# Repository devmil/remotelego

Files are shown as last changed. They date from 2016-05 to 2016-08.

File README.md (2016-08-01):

# Remote Lego project
This project contains all the bits needed to make a remote controllable (Lego) car model.

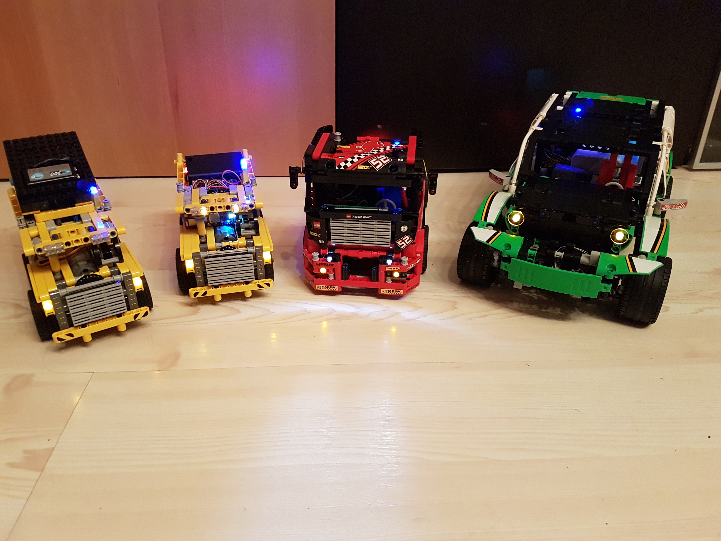
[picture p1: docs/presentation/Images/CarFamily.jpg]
Lego car family


For a guide how to modify and build the physical part of this project please refer to the project page on Hackster.io ([Project page](https://www.hackster.io/projects/9b59a9))
It contains instructions and a BOM for what is needed to get a remote controllable (Lego) car model.

The repository consists of two main parts:
##[Embedded](embedded/README.md)
This is where all the code resides that is needed for the embedded car electronics. It contains code for the mainboard as well as for the control board.

## Remote control applications
There are some remote control applications available for controlling the car model:
- [**Android / Android Wear**](android/README.md)
This simple app consists of a smartphone application and a wearable application
- [**Tizen wear**](tizen/wear/README.md)
Contains a Tizen Wear app
- [**WebApp**](https://github.com/devmil/remotelego_app)
The WebApp is hosted in a separate Repository as the distributed version gets hosted on GitHub. If you only want to control your model then you simply can use the already deployed version of this app.

# Getting started
After preparing your model you want to control and after creating a Mainboard (either by using a pre-made PCB or a perfboard) you can start off putting software onto your controllers.
Please refer to each components ReadMe to get a compile and flash guide:
- [ATMega32](embedded/Atmega/README.md)
- [RedBear DUO](embedded/RedBearDuo/README.md)
- [BLE Nano](embedded/BLENano/README.md)

For testing you can either use the WebApp (if you have an Android 6 device with Chrome and set it up correctly) or (more easier to set up) use the [Android app](android/README.md)

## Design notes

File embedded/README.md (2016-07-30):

# Remote Lego - Embedded
This subtree contains all the source code needed for the various embedded controllers that are part of the (Lego) remote controlled car.

##[Mainboard (Atmega)](Atmega/README.md)
The mainboard contains an Atmega microcontroller that is responsible for all the low level hardware communication. It configures timers to generate PWM signals, sets Pins for switching LEDs on and off and has some additional mechanisms to ensure that the car isn't driving away when the connection is lost or the control board hangs up :)
It gets controlled by the RedBear Duo (or any other controller you might use) via serial commands.

##[RedBear Duo](RedBearDuo/README.md)
The Duo is the communication partner for all remote controls. It provides the Bluetooth service needed for communication with the model and it contains all the car specific information (in form of profiles) like maximum steering angle, supported features, steering offset, ...

##[BLE Nano](BLENano/README.md)
This little helper has only one task: Broadcast the Eddystone advertising package. The software for it is designed in a way that it is generic and receives the URI to broadcast via serial commands.

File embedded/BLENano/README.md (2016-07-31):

# Remote Lego - Embedded - Control board (BLE Nano)

The BLE Nano is a Eddystone Broadcaster. It gets the URI to broadcast via UART following the same communication protocol used between RedBear DUO and the Mainboard.

For a guide how to set up the Arduino IDE to work with the BLE Nano see this web page: https://github.com/RedBearLab/nRF51822-Arduino

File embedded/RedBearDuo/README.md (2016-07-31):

# Remote Lego - Embedded - Control board (RedBear DUO)

Control board

The RedBear duo is the brain of the car models. It contains all the car specific logic and is the communication partner for the remote control. It implements the GATT service to expose the car models features.

## Preparation
In order to flash the software to the RedBear duo you have to install the Arduino IDE, set up the correct RedBear blugin and flash the correct firmware to the DUO.

For a Getting Started guide that covers the installation of Arduino and the RedBear plugin refer to this web page: [https://github.com/redbear/Duo/blob/master/docs/getting_started_with_arduino_ide.md](https://github.com/redbear/Duo/blob/master/docs/getting_started_with_arduino_ide.md)

Please make sure that you select the correct version of the plugin. The version the current code is tested with is mentioned in the LegoControl.ino file on the top.
To isntall the correct firmware for the selected plugin version just use the Arduino mechanism mentioned in the Getting Started guide to flash the firmware.

Additionally you need to install an stl port for Arduino as the lego car code uses standard types (shared_ptr, vector). There is a zip file containing the Arduino in the repository but you can just follow this guide to download and install the stl port:
[https://github.com/vancegroup/stlport-avr/wiki](https://github.com/vancegroup/stlport-avr/wiki).

## Flash
After you have set up the environment and installed the correct firmware version you should be ready to go. Just hit "Upload" in the Arduino IDE to compile the project and upload it to the RedBear Duo.

## Inner workings
The RedBear Duo code consists of

1. The LegoControl.ino file
This file is only used as an entry point. The system initialization is triggered there and the main cycle gets distributed. All other files are C++ files.

2. AVRCommunication.
This module encapsulates all communication logic with the AVR. It exposes the available commands via CommandData factory methods so that no other module has to know the inner structure of these commands. It also handles the serial protocol used to communicate with the AVR.

3. BLECommunication
This module contains the GATT service configuration and the implementation of the Service and the Characteristics. Here the Link between the Bluetooth communication and the model is made.

4. BlinkControl
This module handles the Blink logic. It controls the central Blink timer and triggers a re-send of the AVR telegrams

5. Bluetooth
This modules creates an abstraction layer on top of the Bluetooth API provided by RedBear. It works with Service and Characteristic classes, handles the advertisement bytes and routes read/write requests to the correct characteristic instance.

6. LegoCarModel
The LegoCarModel is the heart of the car. It contains all the business logic and contains the current car state. Any changes made to the state of the model get translated into according AVR telegrams and get sent to the Mainboard.

7. NanoCommunication
This module encapsulates the communication with the BLW Nano. It basically sends the Eddystone URI to the BLE Nano (or better: ensures that the current URI is transmitted to the BLE Nano). It does so cyclic as the protocol isn't as strict as with the AVRCommunication so that the timeouts are smaller and therefore a immediate transmittion can't be guarantieed. This has been done to not disturb the AVR communication when there is a problem with the BLE Nano communication (e.g. when the module is missing)

8. Profiles
Each car model has its own specifics. These specifics are provided by instances of "ICarProfile". Each car model that we have controlled using this mechanism already has a profile. For the code to compile you have to choose a profile (or create your own).
Some of the specifics are: 
 - maximum steering angle
 - steering offset
 - steering inverted?
 - Available features

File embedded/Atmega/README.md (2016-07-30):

# Remote Lego - Embedded - Mainboard (Atmega)

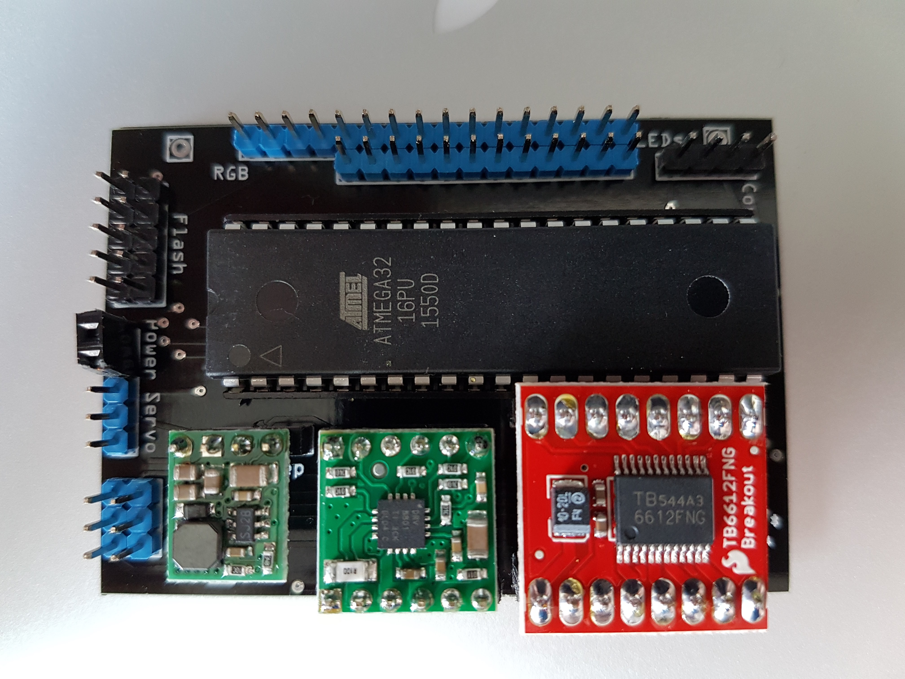
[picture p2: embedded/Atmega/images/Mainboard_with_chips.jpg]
Mainboard


The Mainboard is designed to be generic. It doesn't have any car specific logic. For example: It even doesn't have the logic to switch on the reverse driving lights when driving backwards. 

The idea behind that is to have a fully generic Mainboard with a very stable software and (hopefully) no variance at all.

## Prerequisites
In order to build and flash the software to the AVR you need to install:
###AVR toolchain
Installation depends on your development machine. For Mac just use homebrew and install it by executing:

`brew install avr-libc`

This toolchain should contain avr-gcc and avrdude
### Make
If you have a Mac make is part of XCode. Just make sure you have it installed.
On other machines you have to install make by using a package manager or setup.

###Burn AVR
The AVR has to be configured one time. To do that, plug the flash adapter cable to the mainboard and power it on. Please check the plug if the nose heads away from the mainboard (see picture)
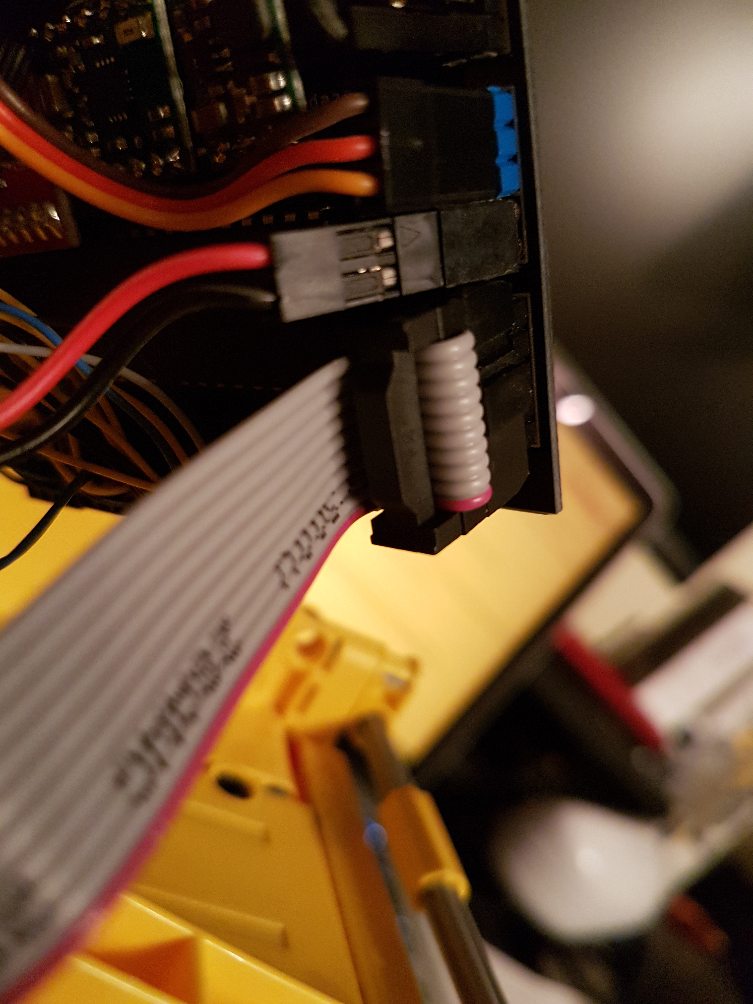
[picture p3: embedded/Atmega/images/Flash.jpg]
Flash plug

Use a Terminal application of your choice, go to the main directory and execute 

`make prepare_avr`

## Build
Open your favourite Terminal, go to the main directory and enter

`make all` or `make rebuild`

## Flash
Make sure you have connected the AVT flash USB device to the Mainboard and that you have powered it up. Please check the plug if the nose heads away from the mainboard (see picture)
Open your favourite Terminal, go to the main directory and enter

`make flash`

## How it works
The AVR gets commands via UART and executes them.

It also awaits a periodical ping from the control module otherwise it switches everything off (speed, steering, ...) to make sure that a control module crash doesn't lead to a car that drives away :)

The only thing the Mainboard persists is the steering offset. As soon as the Control board sends a steering offset the AVR stores it to the EEPROM. This is done to have no strange behavior during boot (The AVR is immediately up and centers the servo. When the control module is up it sends the offset which leads to another angle (when offset !=0).

The AVR uses all 4 timer channels. One for the main motor, two for the feature motors and one for the servo. The servo timer is also used to update the internal clock and to make periodical checks (like if the feature motor timeout has been reached)

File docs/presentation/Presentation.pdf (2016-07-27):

# PHYSICAL WEB MEETS WEB BLUETOOTH

## RC LEGO CAR PROJECT

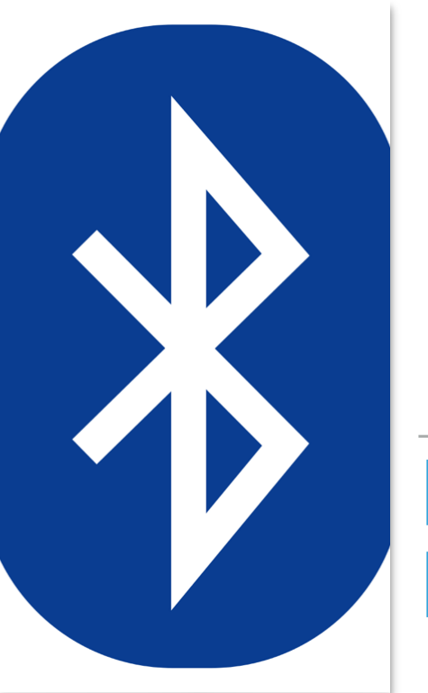
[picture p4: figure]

# BLUETOOTH BACKGROUND

BLUETOOTH BACKGROUND

GENERAL INFORMATION

▸ developed 1990
▸ standard for wireless device to device communication
▸ current version: v4.2
▸ „normal“ Bluetooth connection oriented (pairing)
▸ Bluetooth Low Energy (since v4.0) ad hoc communication possible

3

BLUETOOTH BACKGROUND

BLUETOOTH PROFILES

▸ Interface definitions. Samples are:
▸ A2DP (Advanced Audio Distribution Profile) - audio streaming
▸ OBEX-FTP - file transfer
▸ HID - Human Interface Device Profile
▸ PAN - Personal Area Network Profile ▸ GATT - Generic Attribute Profile

4

BLUETOOTH BACKGROUND

BLUETOOTH LOW ENERGY

▸ Since Bluetooth v4.0
▸ Optional (v4.0 devices don’t have to support BLE)
▸ Physical wireless communication is different for Bluetooth and BLE so most Bluetooth chips have two circuits
▸ Slaves send advertisement packages periodically
▸ only GATT profiles supported
▸ Android: since Version 4.3, iOS: since Version 5

5

BLUETOOTH BACKGROUND

BLUETOOTH GATT PROFILE

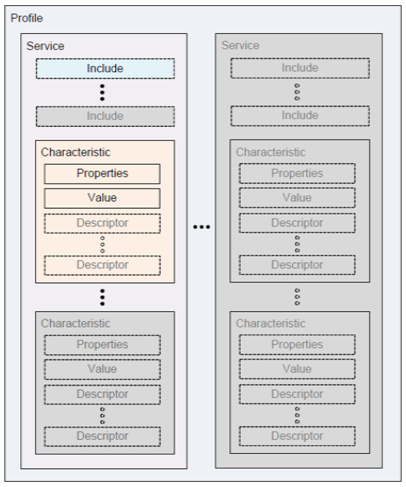
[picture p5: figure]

▸ A device implementing the GATT profile provides: ▸ 1..n services [UID]
▸ with 1..n characteristics [UID] ▸ read/write/readWrite
▸ Represents a value
▸ There are a number of standardized services (standardized UID):
▸ Battery Service
▸ Blood Preassure

▸ …

6

BLUETOOTH BACKGROUND

BLUETOOTH BEACONS

▸ Based on Bluetooth Low Energy

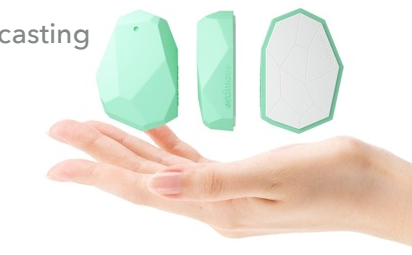
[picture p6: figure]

▸ Continuous advertisement package broadcasting ▸ Protocols
▸ iBeacon (Apple): UID advertisement
▸ AltBeacon: UID advertisement
▸ URIBeacon: URL advertisement
▸ Eddystone (Google): UID, URL or TLM advertisement
▸ Clients use the beacons to react to their presence and / or data

7

BLUETOOTH BACKGROUND

PHYSICAL WEB

▸ Initiated by Google

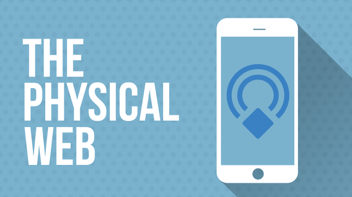
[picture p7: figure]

▸ Idea: Interaction with a nearby device should be possible without installing anything on the client device
▸ Based on Eddystone Beacons (currently, the idea is independent from that)
▸ Integration in Android devices is currently rolling out (newest Google Play Services -> Nearby)
▸ Usable with the Physical Web app (Android) or Google Chrome (iOS)

8

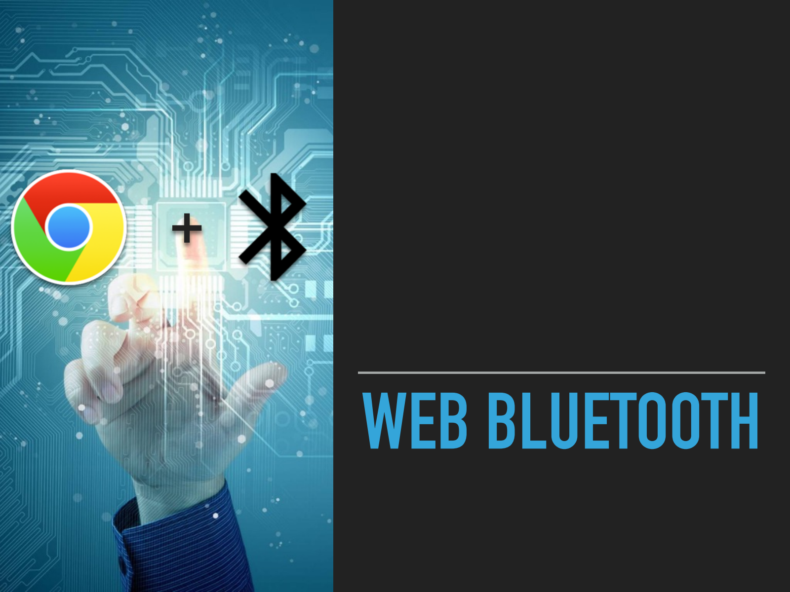
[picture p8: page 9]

# WEB BLUETOOTH

+

WEB BLUETOOTH

CORNERSTONES

▸ Standard for interacting with BLE devices from a web page via JavaScript (WebApp)
▸ Developed as a community team managed from the W3C ▸ No standard yet and no plans in sight
▸ Many years will pass until WebBluetooth is a standard and integrated in all common browsers and platforms

10

WEB BLUETOOTH

CURRENT PROGRESS

▸ Google has done a first reference implementation in Chrome/ Chromium
▸ Work in progress: API can change any time
▸ Only a hand full of platforms supported (27.06.16: Android, Chrome OS, Linux, planned: Windows, MacOS, iOS: when Apple adds WebBluetooth to its WebKit)
▸ Microsoft is thinking about an implementation („under consideration“)
▸ Apple didn’t release any statement regarding WebBluetooth yet

11

WEB BLUETOOTH

SECURITY

▸ Protection against abusing this API is the primary goal of the specification
▸ Requirement: User has to actively interact with the device to provide a web application access to a BLE device
▸ The web app can’t see all BLE devices. It only gets access to the device the user selected (so that location determination isn’t possible using this API)
▸ API only can be used having a secure connection (https)

12

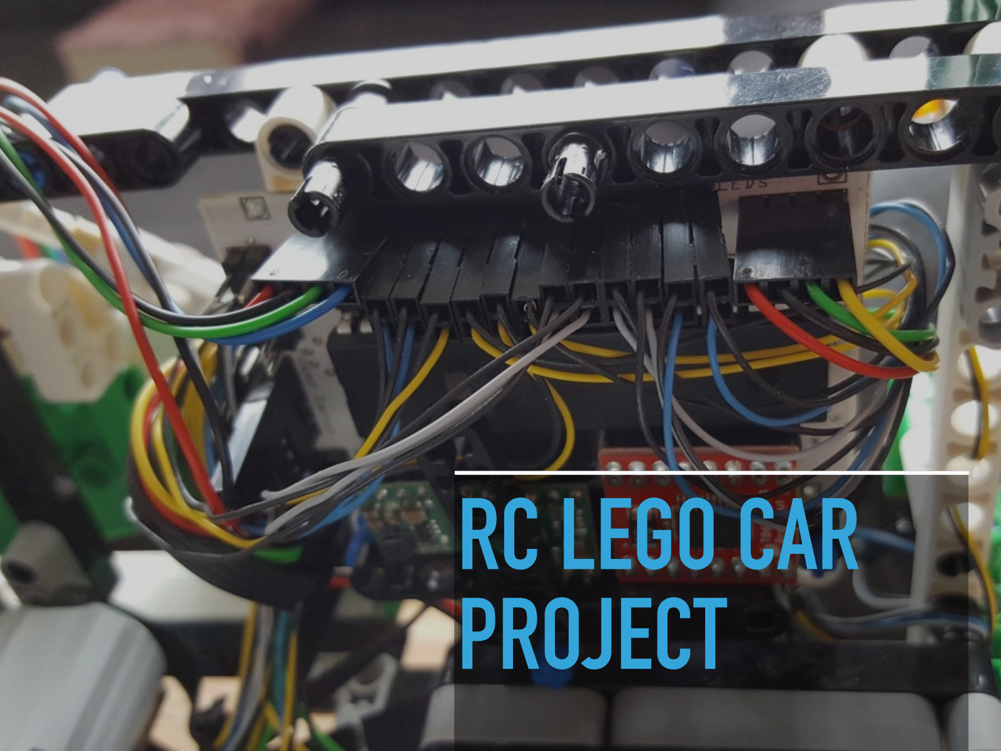
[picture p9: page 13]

# RC LEGO CAR PROJECT

RC LEGO CAR PROJECT

INTENTION

▸ Combine WebBluetooth with the ideas from the Physical Web
▸ Controlling a device
▸ without installing an app
▸ without having the device to be connected to the internet
▸ using state of the art web technology like offline caching

14

RC LEGO CAR PROJECT

WHY LEGO?

▸ First try: Switching a LED on and off
▸ BLE Slave: Raspberry Pi (NodeJS)
▸ Not very impressive => the idea to control a Lego Technic car has been born
▸ Project mutated from a web to a electronic project

15

RC LEGO CAR PROJEKT

VARIANTS

▸ Over the course of the project different variants were implemented ▸ BLE Slave (Car logic):
▸ Raspberry Pi (NodeJS)
▸ Intel Edison (NodeJS)
▸ RedBear Duo (Arduino) and ATMega32 (C)
▸ BLE Master (Remote control)
▸ Android App (Java, Android Framework)
▸ Android Wear App (Java, Android Framework)
▸ Tizen Wear App (HTML 5, TAU [Tizen Advanced UI]) ▸ Web App (HTML 5, AngularJS 2)

16

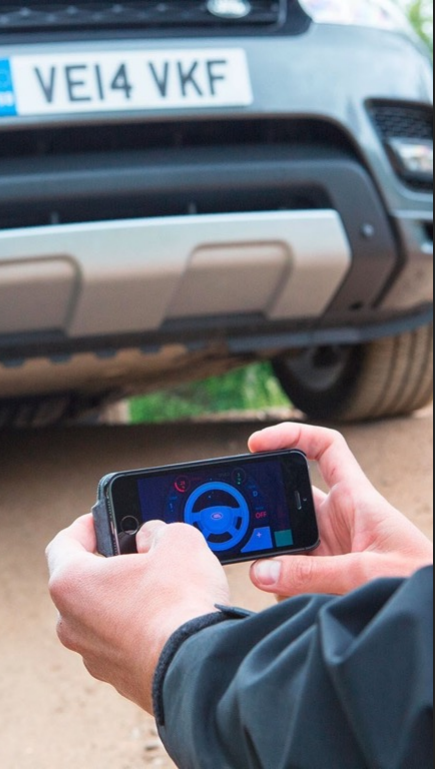
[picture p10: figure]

# REMOTE CONTROL

## RC LEGO CAR PROJECT

RC LEGO CAR PROJECT - REMOTE CONTROL

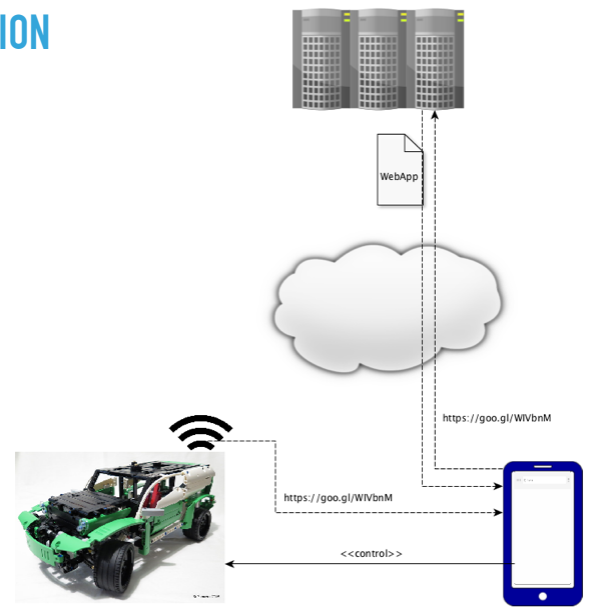
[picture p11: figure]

CONNECTION

18

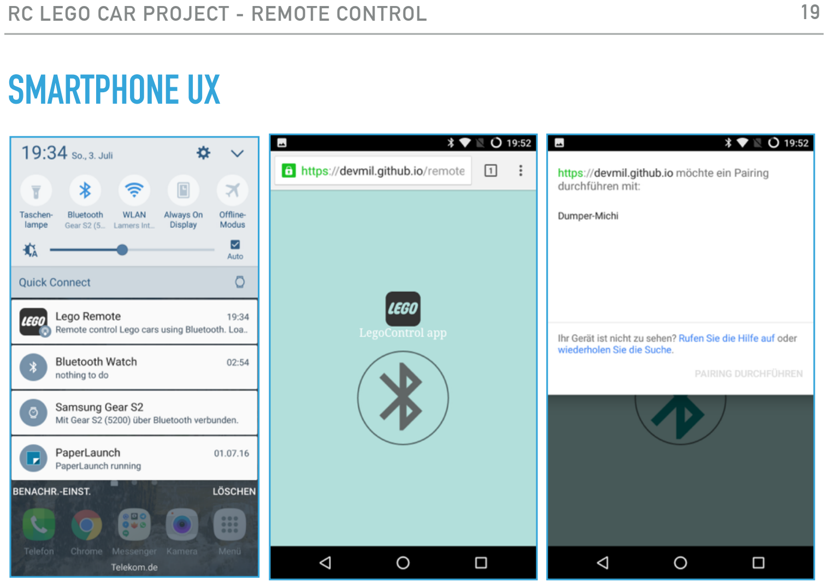
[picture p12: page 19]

RC LEGO CAR PROJECT - REMOTE CONTROL

SMARTPHONE UX

19

RC LEGO CAR PROJECT - REMOTE CONTROL

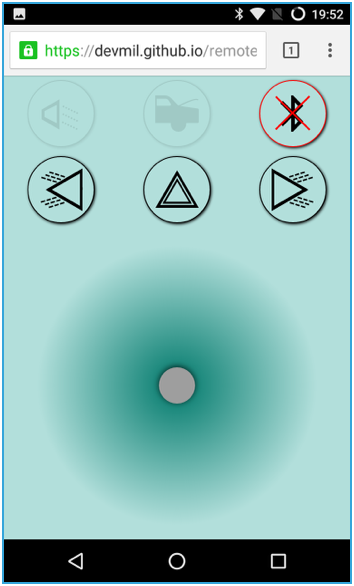
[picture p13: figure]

WEBAPP

▸ Typescript
▸ AngularJS 2
▸ Connects to the Lego control service (via UID) ▸ Writes data to characteristics:
▸ SpeedCharacteristic
▸ SteeringCharacteristic
▸ TrunkCharacteristic
▸ FrontLightCharacteristic ▸ BlinkCharacteristic

20

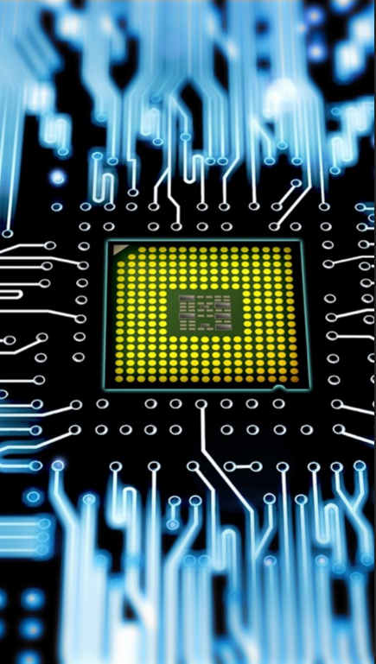
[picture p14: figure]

# CAR ELECTRONICS

## RC LEGO CAR PROJECT

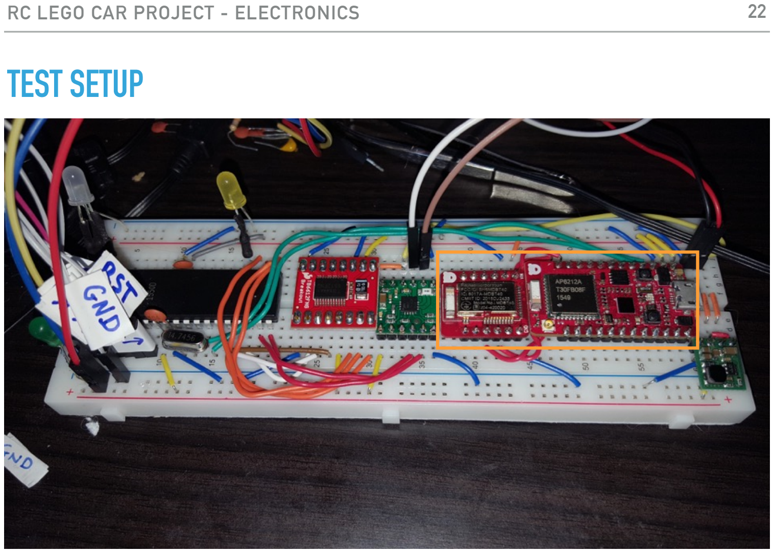
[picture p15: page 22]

RC LEGO CAR PROJECT - ELECTRONICS

TEST SETUP

22

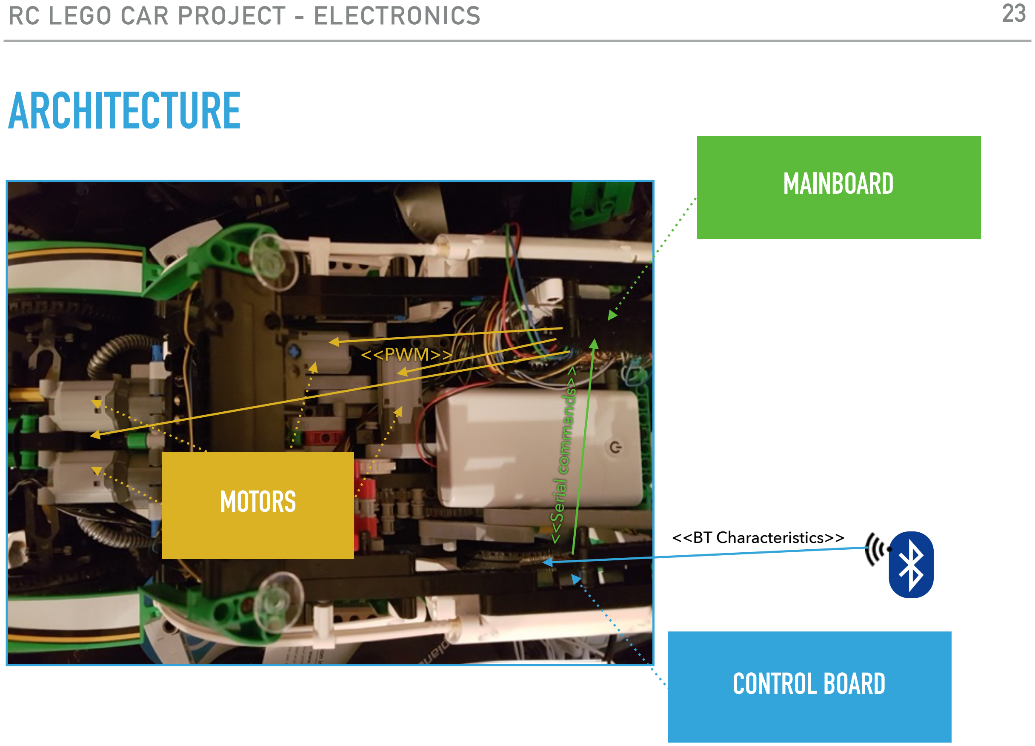
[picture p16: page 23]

RC LEGO CAR PROJECT - ELECTRONICS

ARCHITECTURE

23

<<Serial commands>>

<<BT Characteristics>>

<<PWM>>

CONTROL BOARD

MAINBOARD

MOTORS

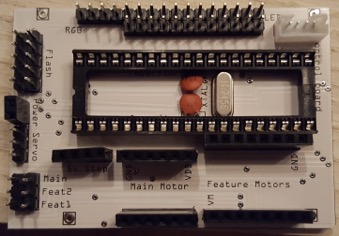
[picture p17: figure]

RC LEGO CAR PROJECT - ELECTRONICS

MAINBOARD

▸ Hardware control
▸ No car specific logic

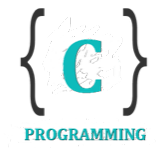
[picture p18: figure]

▸ Timer for PWM signals
▸ Parts:
▸ ATMega32
▸ 5V Step down regulator

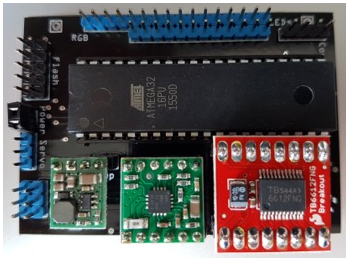
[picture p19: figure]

▸ H bridges (single for main motor, dual for feature motors) ▸ Receives commands via UART from control board

24

RC LEGO CAR PROJECT - ELECTRONICS

MAINBOARD CIRCUIT

25

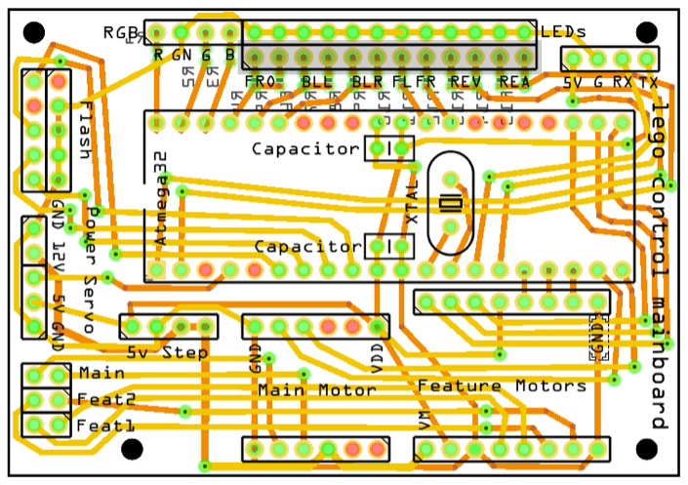
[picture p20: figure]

RC LEGO CAR PROJECT - ELECTRONICS

CONTROL BOARD

▸ Provides the BT service
▸ Contains the car logic
▸ what does „open trunk“ mean?

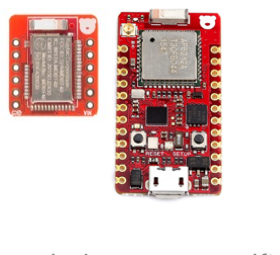
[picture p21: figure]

▸ Blink control (sends LED on/off to the mainboard, controls the timings itself) ▸ has a car specific profile
▸ Maximum steering angles
▸ is steering inverted?
▸ is Trunk, Front light, Blinking, … supported? ▸ Broadcasts the Eddystone telegram that contains the URL to the WebApp

26

RC LEGO CAR PROJECT - ELECTRONICS

INFORMATION FLOW

27

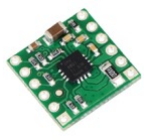
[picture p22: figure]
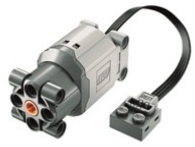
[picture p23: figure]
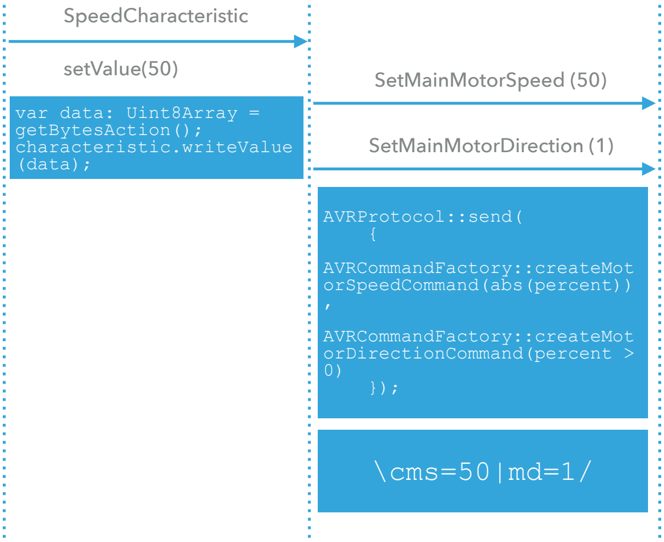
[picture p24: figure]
SpeedCharacteristic; setValue(50); var data: Uint8Array = getBytesAction(); characteristic.writeValue (data);; SetMainMotorSpeed (50); SetMainMotorDirection (1); AVRProtocol::send( {; AVRCommandFactory::createMot orSpeedCommand(abs(percent)) ,; AVRCommandFactory::createMot orDirectionCommand(percent > 0); \cms=50|md=1/

50% PWM (12V)

50% PWM (12V)

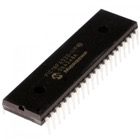
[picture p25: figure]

50% PWM (5V)

Direction Pin High

float value = (motor-
>timerMax *
percent) / 100;
*motor->
timerCounterRegister8
= (uint8_t)value;
Pin_setValue(&motor->
pinDirection1,
directionVal);


# DEMO

## RC LEGO CAR PROJECT

RC LEGO CAR PROJECT - SOURCES

SOURCES

▸ Wikipedia
▸ Bluetooth: https://de.wikipedia.org/wiki/Bluetooth
▸ BLE: https://de.wikipedia.org/wiki/Bluetooth_Low_Energy
▸ Bluetooth developer
▸ GATT: https://developer.bluetooth.org/TechnologyOverview/Pages/GATT.aspx (https://developer.bluetooth.org/TechnologyOverview/Pages/GATT.aspx)
▸ Physical Web
▸ https://google.github.io/physical-web/

29


RC LEGO CAR PROJECT - SETUP

SETUP (ANDROID 6.0, CHROME)

30

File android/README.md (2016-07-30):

# Remote Lego - Android remote control
App screenshot

The lego remote control app contains three modules:

1. **app**
The Android smartphone application. It needs Android Lollipop+ (21+) because it uses the BLE API.

2. **legologic**
This module gets used by the app and the legowear module. It contains the communication bits with the remote car and the control UI.

3. **legowear**
The Android wear application using (as well as the app) the legologic bits to display the control UI and communicating with the (Lego) car model

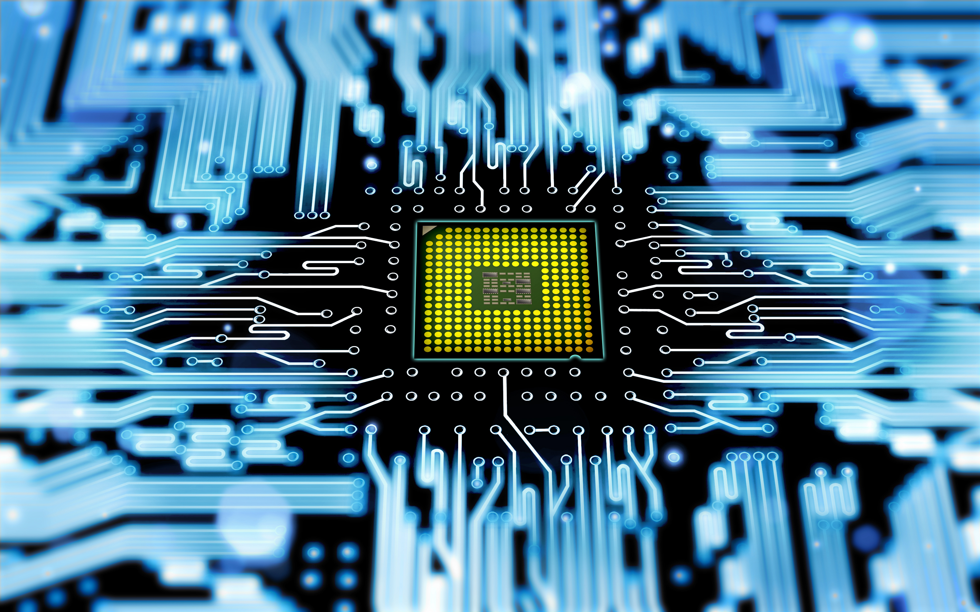
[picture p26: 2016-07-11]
docs/presentation/Images/Electronics.jpg

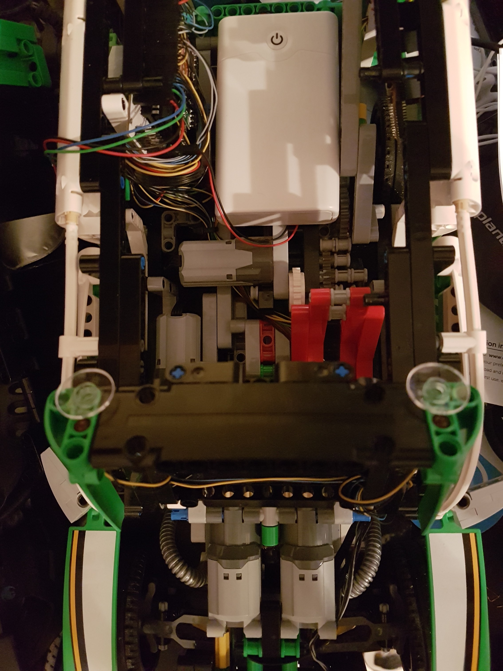
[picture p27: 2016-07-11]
docs/presentation/Images/RC Car Overview.jpg

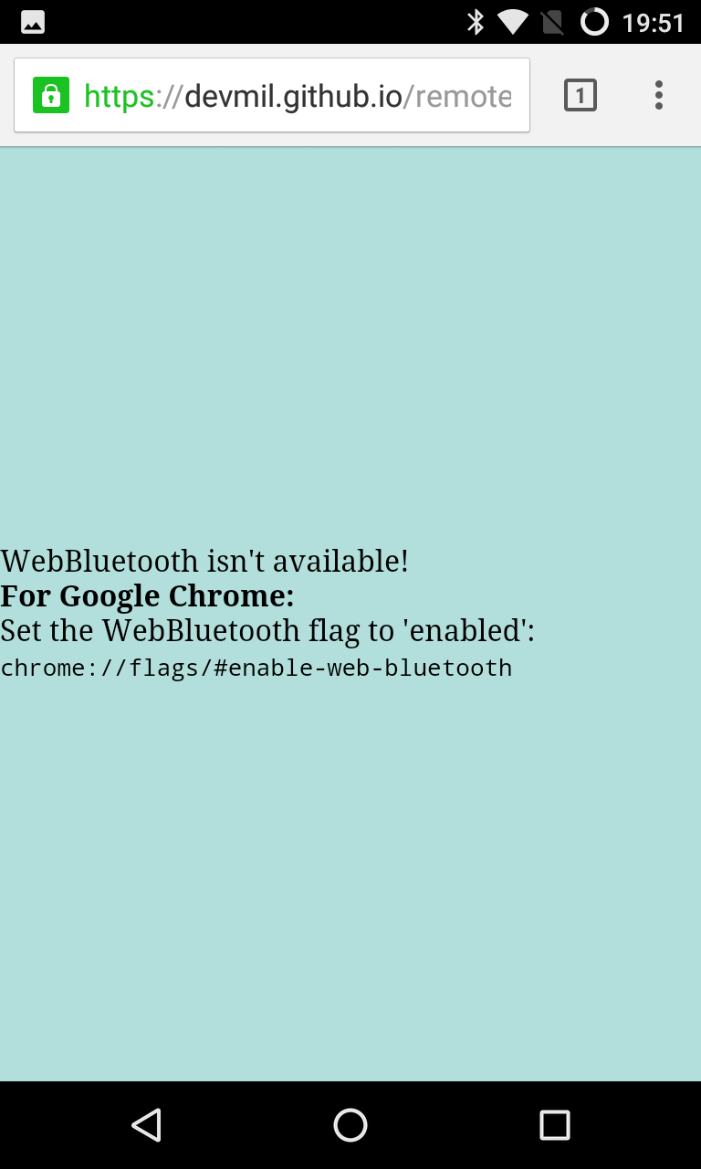
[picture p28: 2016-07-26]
docs/presentation/Images/Chrome_1_Message.png

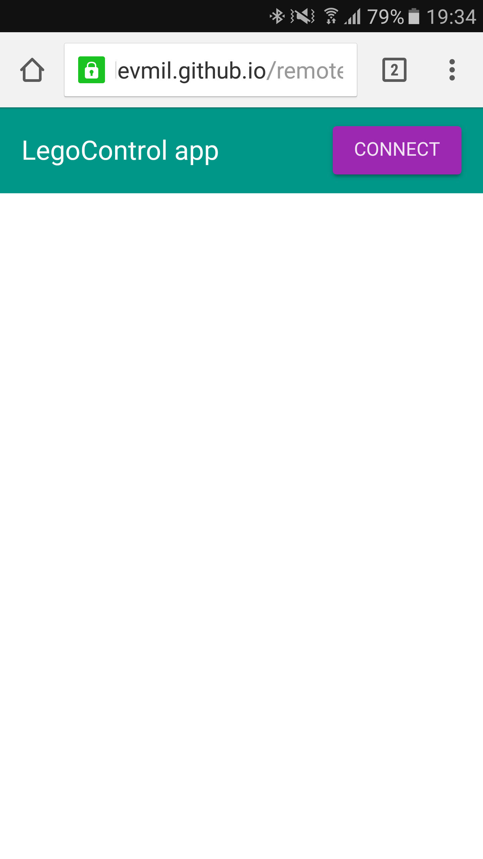
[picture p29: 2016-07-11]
docs/presentation/Images/Screenshot_20160703-193430.png

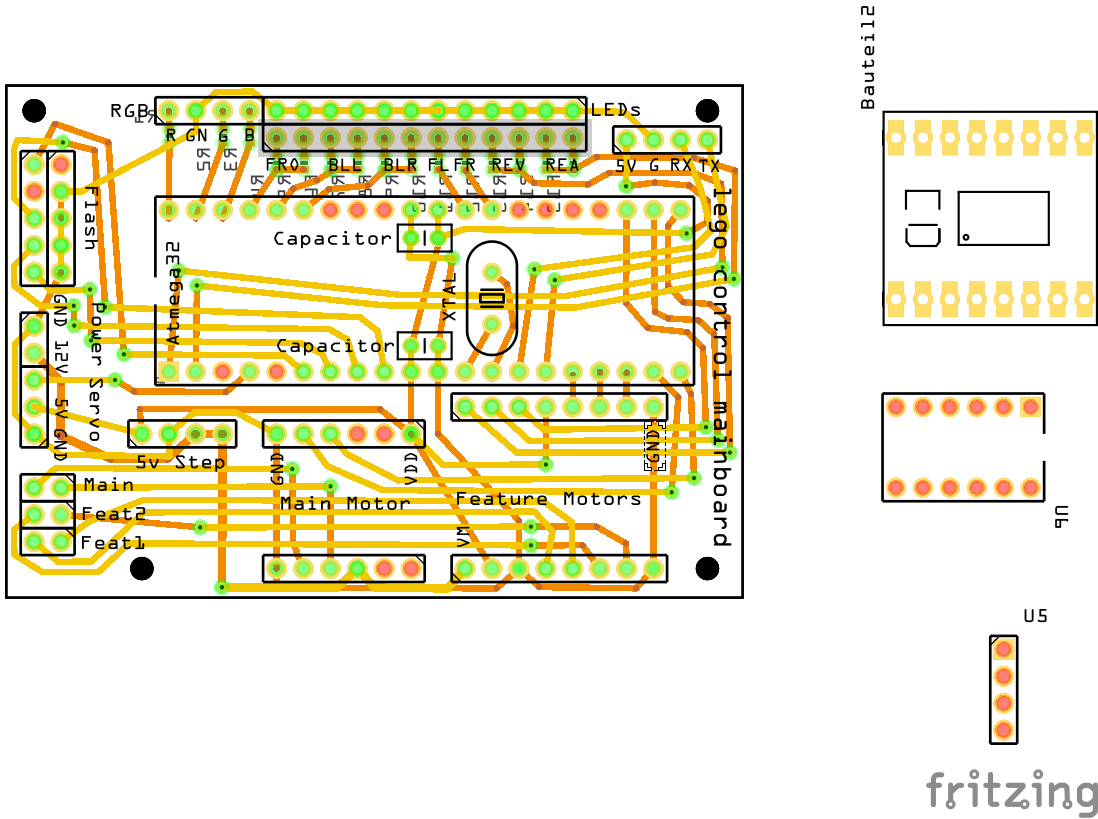
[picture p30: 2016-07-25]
docs/presentation/Images/Mainboard_Leiterplatte.png

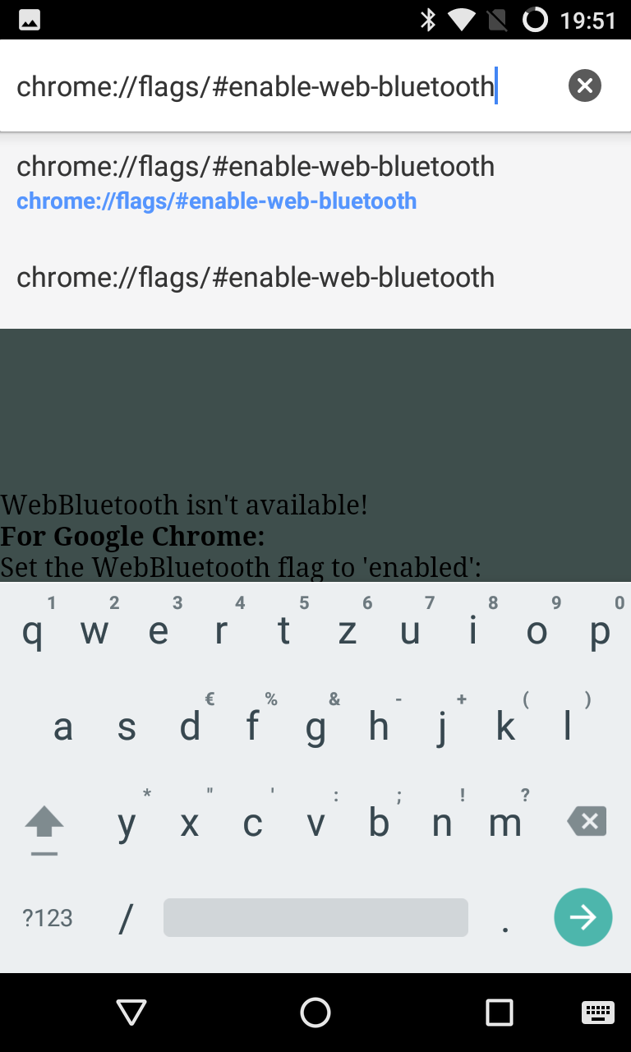
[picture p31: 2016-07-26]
docs/presentation/Images/Chrome_2_Flags.png

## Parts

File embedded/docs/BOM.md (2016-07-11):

#Lego RC electronics BOM

##General
- cables in different colors (Mainboard -> LEDs, Motors, Control board)
- a bunch of Dupont plugs (2 pin, 4 pin)
- Dupont capable crimping tool
- soldering iron & accessories
- AVR flash adapter

##Control Module variant a (Redbear Duo, BLE Nano)
- Redbear Duo (25€)
- BLE Nano (15€)
- circuit board
- lacquered wire for soldering connections on the circuit board

##Control module variant b (Raspberry Pi)
- Raspberry Pi 1/2/3 (35€)
- two RPI compatible Bluetooth USB dongles (10€ each)
- Battery pack to power the RPi (10€)

##Mainboard
- Atmel ATMega32 16PU or pin compatible (6€)
- Pololu 5V, 600mA Step-Down Voltage Regulator (D24V6F5) (6€)
- Pololu Single Brushed Motor Driver Carrier (DRV8801) (Main motor) (6€)
- Sparkfun Dual Motor Driver 1A TB6612FNG (9€)
- 14,745 MHz quartz
- 2x 100nF capacitor
- 15x SMD resistors (470 Ohm)
- a bunch of pin headers (male/female)
- a bunch of LEDs (2x front light, 2x back light, 2x rear light, 2x front fog lights, 4x blinking lights, 1x RGB state led)

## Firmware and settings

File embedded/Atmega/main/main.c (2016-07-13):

#include <avr/io.h>
#include <avr/interrupt.h>	// include interrupt support
#include <avr/wdt.h>
#include <avr/eeprom.h>
#include <util/delay.h>
#include <stdlib.h>
#include <string.h>

#include "uart.h"
#include "clock.h"
#include "pin.h"
#include "led.h"
#include "motor.h"

//For B0: BIT(B,0)
#define BIT(p,b)                (P##p##b)
#define PORT(p)                 (PORT##p)
#define DDR(p)                  (DDR##p)

#define INIT_PIN(port, bit) { .definitionRegister = &DDR(port), .portRegister = &PORT(port), .offset = BIT(port, bit) }
#define D_PIN(name, port, bit) Pin PIN_##name = INIT_PIN(port, bit);


                              /*  ----------------------------  */
D_PIN(LED_REVERSE,     B, 0)  /* -|           \____/         |- */ D_PIN(LED_STATE_R,     A, 0)
D_PIN(LED_REAR,        B, 1)  /* -|                          |- */ D_PIN(LED_STATE_G,     A, 1)
D_PIN(LED_DEBUG,       B, 2)  /* -|                          |- */ D_PIN(LED_STATE_B,     A, 2)
D_PIN(SERVO_SIGNAL,    B, 3)  /* -|                          |- */ D_PIN(LED_FRONT_H,     A, 3)
/*        SS              */  /* -|                          |- */ D_PIN(LED_BLINK_L,     A, 4)
/*        MOSI            */  /* -|                          |- */ D_PIN(LED_BLINK_R,     A, 5)
/*        MISO            */  /* -|                          |- */ /*  A6                    */
/*        SCK             */  /* -|                          |- */ /*  A7                    */
/*        RESET           */  /* -|                          |- */ /*        AREF            */
/*        VCC             */  /* -|                          |- */ /*        GND             */
/*        GND             */  /* -|                          |- */ /*        AVCC            */
/*        XTAL2           */  /* -|                          |- */ D_PIN(LED_FRONT_F_L,   C, 7)
/*        XTAL1           */  /* -|                          |- */ D_PIN(LED_FRONT_F_R,   C, 6)
/*        RXD             */  /* -|                          |- */ /*  C5                    */
/*        TXD             */  /* -|                          |- */ /*  C4                    */
D_PIN(FEATURE1_DIR2,   D, 2)  /* -|                          |- */ /*  C3                    */
D_PIN(FEATURE1_DIR1,   D, 3)  /* -|                          |- */ D_PIN(LED_DEBUG2,      C, 2)
D_PIN(FEATURE1_PWM,    D, 4)  /* -|                          |- */ D_PIN(FEATURE2_DIR2,   C, 1)
D_PIN(MAIN_PWM,        D, 5)  /* -|                          |- */ D_PIN(FEATURE2_DIR1,   C, 0)
D_PIN(MAIN_DIR1,       D, 6)  /* -|                          |- */ D_PIN(FEATURE2_PWM,    D, 7)
                              /*  ----------------------------  */

#define SERVO_PRESCALER 			1024
#define SERVO_PRESCALER_BITS		(1<<CS00) | (1<<CS02)
#define SERVO_TIMER_TICKS			255
#define SERVO_EFFECTIVE_F			(F_CPU / SERVO_PRESCALER) //14745000 / 1024 = 14399
#define SERVO_TIMER_PERIOD_MS		(((float)1000 * SERVO_TIMER_TICKS) / SERVO_EFFECTIVE_F)	//(1000 * 255) / 14399 = 17,70956316410862
#define SERVO_TIMER_MS_PER_TICK		(SERVO_TIMER_PERIOD_MS / SERVO_TIMER_TICKS) //0,06944926731023
#define SERVO_MIN_MS				0.8f
#define SERVO_MAX_MS				2.3f

#define MAIN_MOTOR_PRESCALER		/*	8			*//*	1			*/	64						
#define MAIN_MOTOR_PRESCALER_BITS	/*	(1<<CS11)	*//*	(1<<CS10) 	*/	(1<<CS11) | (1<<CS10)	
#define MAIN_MOTOR_TIMER_TICKS		255

#define FEAT_MOTOR_PRESCALER		/*	8			*//*	1         	*/	64						
#define FEAT_MOTOR_PRESCALER_BITS	/*	(1<<CS21)	*//*	(1<<CS20) 	*/	(1<<CS21) | (1<<CS10)	
#define FEAT_MOTOR_TIMER_TICKS		255

#define UART_BAUDRATE				115200

#define RECEIVER_BUFF_SIZE 			128

#define CONTROLLER_TIMEOUT_MS		1000

//Commands
const char* COMMAND_PING 						= "pp";

const char* COMMAND_STEERING_OFFSET_PERCENT		= "sso";

const char* COMMAND_SERVO_PERCENT 				= "sp";

const char* COMMAND_MOTOR_SPEED 				= "ms";
const char* COMMAND_MOTOR_DIRECTION				= "md";

const char* COMMAND_STATUS_COLOR				= "sc";

const char* COMMAND_SET_FRONT_HEADLIGHT			= "sfh";
const char* COMMAND_SET_REAR_LIGHT				= "srl";
const char* COMMAND_SET_FRONT_FOGLIGHT_LEFT		= "sffl";
const char* COMMAND_SET_FRONT_FOGLIGHT_RIGHT	= "sffr";
const char* COMMAND_SET_FRONT_FOGLIGHT			= "sff";
const char* COMMAND_SET_REVERSING_LIGHT			= "srel";
const char* COMMAND_SET_BLINK_LIGHT_LEFT		= "sblll";
const char* COMMAND_SET_BLINK_LIGHT_RIGHT		= "sbllr";

const char* COMMAND_FEAT1_MOTOR_SPEED 			= "fm1s";
const char* COMMAND_FEAT1_MOTOR_DIRECTION		= "fm1d";
const char* COMMAND_FEAT1_MOTOR_TIMEOUT_S		= "fm1ts";
const char* COMMAND_FEAT1_MOTOR_TIMEOUT_MS		= "fm1tms";

const char* COMMAND_FEAT2_MOTOR_SPEED 			= "fm2s";
const char* COMMAND_FEAT2_MOTOR_DIRECTION		= "fm2d";
const char* COMMAND_FEAT2_MOTOR_TIMEOUT_S		= "fm2ts";
const char* COMMAND_FEAT2_MOTOR_TIMEOUT_MS		= "fm2tms";

uint8_t* EEPROM_ADDR_SERVO_OFFSET		= 0;

int8_t s_servoOffsetPercent;
int8_t s_servoPercent;

void Servo_setPercent(float percent) {
	s_servoPercent = percent;
	percent += s_servoOffsetPercent;
	if(percent > 100) {
		percent = 100;
	}
	if(percent < 0) {
		percent = 0;
	}
	float servoMs = SERVO_MIN_MS + ((SERVO_MAX_MS - SERVO_MIN_MS) * percent) / 100;
	float servoTicks = servoMs / SERVO_TIMER_MS_PER_TICK;
	OCR0 = 255 - (int8_t)servoTicks;
}

void Servo_init() {
	Pin_setMode(&PIN_SERVO_SIGNAL, PinMode_Output); 		// PB3 == OC0 is servo output
	Pin_setValue(&PIN_SERVO_SIGNAL, PinValue_Low); 			//pull down

	TCCR0 |= (1<<WGM00) | (1<<WGM01);		// fast PWM mode
	TCCR0 |= (1<<COM01);					// compare output mode
	TCCR0 |= (1<<COM00);					// non inverted PWM
	TCCR0 |= SERVO_PRESCALER_BITS;

	s_servoOffsetPercent = eeprom_read_byte(EEPROM_ADDR_SERVO_OFFSET);
	if(s_servoOffsetPercent > 45 || s_servoOffsetPercent < -45) {
		s_servoOffsetPercent = 0;
	}

	Servo_setPercent(50);					//center servo	
}

Clock s_clock;
Motor s_mainMotor;
TimeoutMotor s_featureMotor1;
TimeoutMotor s_featureMotor2;
RgbLed s_stateLed;

Pin s_pinEmpty = { 0, 0, 0 };

volatile float s_millisecondsSinceLastControl = 0;
uint8_t s_controllerTimeoutReached = 0;

uint8_t checkControllerTimeoutReached() {
	if(s_controllerTimeoutReached) {
		return s_controllerTimeoutReached;
	}
	if(s_millisecondsSinceLastControl > CONTROLLER_TIMEOUT_MS) {
		s_controllerTimeoutReached = 1;
	}
	return s_controllerTimeoutReached;
}

void resetControllerTimeout() {
	s_millisecondsSinceLastControl = 0;
	s_controllerTimeoutReached = 0;
}

void increaseControllerTimeout(float ms) {
	s_millisecondsSinceLastControl += ms;
}

ISR( TIMER0_OVF_vect )
{
	Clock_tick(&s_clock);
	increaseControllerTimeout(s_clock.tickDurationMs);
	TimeoutMotor_tick(&s_featureMotor1);
	TimeoutMotor_tick(&s_featureMotor2);
}

void initMotorTimer() {
	TCCR1A |= (1 << COM1A0) | (1 << COM1A1); 				//Timer1A: inverting PWM
	TCCR1A |= (1 << COM1B0) | (1 << COM1B1); 				//Timer1B: inverting PWM 
	TCCR1A |= (1 << WGM10); 								//Timer1: Phase correct PWM
	TCCR1B |= MAIN_MOTOR_PRESCALER_BITS; 
	
	Pin_setMode(&PIN_MAIN_PWM, PinMode_Output);				// PD5=OC1A is output
	Pin_setMode(&PIN_FEATURE1_PWM, PinMode_Output); 		// PD4=OC1B is output
	
	TCCR2 |= (1 << COM20) | (1 << COM21); 					//Timer1A: inverting PWM
	TCCR2 |= (1 << WGM20); 									//Timer2: Phase correct PWM
	TCCR2 |= FEAT_MOTOR_PRESCALER_BITS; 

	Pin_setMode(&PIN_FEATURE2_PWM, PinMode_Output);			// PD7=OC2 is output
}

void initMainMotor() {
	Motor_init(&s_mainMotor, PIN_MAIN_DIR1, s_pinEmpty, MAIN_MOTOR_TIMER_TICKS, &OCR1A, 0, 1, MotorMode_SpeedDirection);
}

void initFeatureMotor1() {
	TimeoutMotor_init(&s_featureMotor1, SERVO_TIMER_PERIOD_MS, PIN_FEATURE1_DIR1, PIN_FEATURE1_DIR2, MAIN_MOTOR_TIMER_TICKS, &OCR1B, 0, 1, MotorMode_LeftRightPwm);
}

void initFeatureMotor2() {
	TimeoutMotor_init(&s_featureMotor2, SERVO_TIMER_PERIOD_MS, PIN_FEATURE2_DIR1, PIN_FEATURE2_DIR2, FEAT_MOTOR_TIMER_TICKS, 0, &OCR2, 1, MotorMode_LeftRightPwm);
}

void initStatusLed() {
	RgbLed_init(&s_stateLed, PIN_LED_STATE_R, PIN_LED_STATE_G, PIN_LED_STATE_B);
}

void initLEDs() {
	Pin_setMode(&PIN_LED_FRONT_H, PinMode_Output);
	
	Pin_setMode(&PIN_LED_REAR, PinMode_Output);
	
	Pin_setMode(&PIN_LED_FRONT_F_L, PinMode_Output);
	Pin_setMode(&PIN_LED_FRONT_F_R, PinMode_Output);
	Pin_setMode(&PIN_LED_REVERSE, PinMode_Output);

	Pin_setMode(&PIN_LED_BLINK_L, PinMode_Output);
	Pin_setMode(&PIN_LED_BLINK_R, PinMode_Output);
}

void nextTestStep() {
	PinValue currentValue = Pin_getValue(&PIN_LED_DEBUG);
	Pin_setValue(&PIN_LED_DEBUG, currentValue == PinValue_High ? PinValue_Low : PinValue_High); //toggle debug pin
}

char s_uartRcvBuffer[RECEIVER_BUFF_SIZE + 1];
uint8_t s_uartRcvBufferPos = 0;
uint8_t s_backslashReceived = 0;
uint8_t s_inCommand = 0;

uint8_t handleCommand(char* command, char* value) {
	uint8_t result = 0;
	if(strcmp(command, COMMAND_PING) == 0) {
		result = 1;
	} else if(strcmp(command, COMMAND_STEERING_OFFSET_PERCENT) == 0) {
		int8_t newServoOffset = atoi(value);
		if(s_servoOffsetPercent != newServoOffset) {
		  s_servoOffsetPercent = newServoOffset;
		  eeprom_write_byte(EEPROM_ADDR_SERVO_OFFSET, s_servoOffsetPercent);
		  Servo_setPercent(s_servoPercent);
		}
		result = 1;
	} else if(strcmp(command, COMMAND_MOTOR_SPEED) == 0) {
		double doubleVal = atof(value);
		Motor_setSpeedPercent(&s_mainMotor, (float)doubleVal);
		result = 1;
	} else if(strcmp(command, COMMAND_MOTOR_DIRECTION) == 0) {
		int intVal = atoi(value);
		Motor_setDirection(&s_mainMotor, intVal != 0 ? 1 : 0);
		result = 1;
	} else if(strcmp(command, COMMAND_SERVO_PERCENT) == 0) {
		int intVal = atoi(value);
		Servo_setPercent(intVal);
		result = 1;
	} else if(strcmp(command, COMMAND_STATUS_COLOR) == 0) {
		uint32_t color = strtoul(value, (char**)0, 0);
		RgbLed_setColor(&s_stateLed, color);
		result = 1; 
	} else if(strcmp(command, COMMAND_SET_BLINK_LIGHT_LEFT) == 0) {
		uint8_t on = atoi(value) != 0;
		Pin_setValue(&PIN_LED_BLINK_L, on == 0 ? PinValue_Low : PinValue_High);
		result = 1; 
	} else if(strcmp(command, COMMAND_SET_BLINK_LIGHT_RIGHT) == 0) {
		uint8_t on = atoi(value) != 0;
		Pin_setValue(&PIN_LED_BLINK_R, on == 0 ? PinValue_Low : PinValue_High);
		result = 1; 
	} else if(strcmp(command, COMMAND_SET_FRONT_HEADLIGHT) == 0) {
		int on = atoi(value) != 0;
		Pin_setValue(&PIN_LED_FRONT_H, on == 0 ? PinValue_Low : PinValue_High);
		result = 1; 
	} else if(strcmp(command, COMMAND_SET_REAR_LIGHT) == 0) {
		int on = atoi(value) != 0;
		Pin_setValue(&PIN_LED_REAR, on == 0 ? PinValue_Low : PinValue_High);
		result = 1; 
	} else if(strcmp(command, COMMAND_SET_FRONT_FOGLIGHT_LEFT) == 0) {
		int on = atoi(value) != 0;
		Pin_setValue(&PIN_LED_FRONT_F_L, on == 0 ? PinValue_Low : PinValue_High);
		result = 1; 
	} else if(strcmp(command, COMMAND_SET_FRONT_FOGLIGHT_RIGHT) == 0) {
		int on = atoi(value) != 0;
		Pin_setValue(&PIN_LED_FRONT_F_R, on == 0 ? PinValue_Low : PinValue_High);
		result = 1; 
	} else if(strcmp(command, COMMAND_SET_FRONT_FOGLIGHT) == 0) {
		int on = atoi(value) != 0;
		Pin_setValue(&PIN_LED_FRONT_F_L, on == 0 ? PinValue_Low : PinValue_High);
		Pin_setValue(&PIN_LED_FRONT_F_R, on == 0 ? PinValue_Low : PinValue_High);
		result = 1; 
	} else if(strcmp(command, COMMAND_SET_REVERSING_LIGHT) == 0) {
		int on = atoi(value) != 0;
		Pin_setValue(&PIN_LED_REVERSE, on == 0 ? PinValue_Low : PinValue_High);
		result = 1; 
	} else if(strcmp(command, COMMAND_FEAT1_MOTOR_SPEED) == 0) {
		double doubleVal = atof(value);
		TimeoutMotor_setSpeedPercent(&s_featureMotor1, (float)doubleVal);
		result = 1;
	} else if(strcmp(command, COMMAND_FEAT1_MOTOR_DIRECTION) == 0) {
		int intVal = atoi(value);
		TimeoutMotor_setDirection(&s_featureMotor1, intVal != 0 ? 1 : 0);
		result = 1;
	} else if(strcmp(command, COMMAND_FEAT1_MOTOR_TIMEOUT_S) == 0) {
		int intVal = atoi(value);
		TimeoutMotor_setRemaining(&s_featureMotor1, intVal * 1000);
		result = 1;
	} else if(strcmp(command, COMMAND_FEAT1_MOTOR_TIMEOUT_MS) == 0) {
		int intVal = atoi(value);
		TimeoutMotor_setRemaining(&s_featureMotor1, intVal);
		result = 1;
	} else if(strcmp(command, COMMAND_FEAT2_MOTOR_SPEED) == 0) {
		double doubleVal = atof(value);
		TimeoutMotor_setSpeedPercent(&s_featureMotor2, (float)doubleVal);
		result = 1;
	} else if(strcmp(command, COMMAND_FEAT2_MOTOR_DIRECTION) == 0) {
		int intVal = atoi(value);
		TimeoutMotor_setDirection(&s_featureMotor2, intVal != 0 ? 1 : 0);
		result = 1;
	} else if(strcmp(command, COMMAND_FEAT2_MOTOR_TIMEOUT_S) == 0) {
		int intVal = atoi(value);
		TimeoutMotor_setRemaining(&s_featureMotor2, intVal * 1000);
		result = 1;
	} else if(strcmp(command, COMMAND_FEAT2_MOTOR_TIMEOUT_MS) == 0) {
		int intVal = atoi(value);
		TimeoutMotor_setRemaining(&s_featureMotor2, intVal);
		result = 1;
	}
	return result;
}

uint8_t handleCommands() {
	uint8_t inVal = 0;
	char commandBuff[20] = "";
	char valBuff[20] = "";
	uint8_t numOfCommands = 0;
	for(int i=0; i<s_uartRcvBufferPos; i++) {
		if(s_uartRcvBuffer[i] == '=') {
			inVal = 1;
			continue;			
		}
		else if(s_uartRcvBuffer[i] == '|') {
			if(handleCommand(commandBuff, valBuff)) {
				numOfCommands++;
			}
			commandBuff[0] = '\0';
			valBuff[0] = '\0';
			inVal = 0;
			continue;
		}
		else if(inVal) {
			uint16_t idx = strlen(valBuff);
			valBuff[idx] =  s_uartRcvBuffer[i];
			valBuff[idx + 1] = '\0';
		} else {
			uint16_t idx = strlen(commandBuff);
			commandBuff[idx] =  s_uartRcvBuffer[i];
			commandBuff[idx + 1] = '\0';
		}
	}
	if(handleCommand(commandBuff, valBuff)) {
		numOfCommands++;
	}
	uart_puts("\r\n\\r");
	uart_puts("nc=");
	char buff[12];
	itoa(numOfCommands, buff, 10);
	buff[11] = '\0';
	uart_puts(buff);
	uart_puts("/\r\n");
	
	s_inCommand = 0;
	s_uartRcvBufferPos = 0;
	
	return numOfCommands;
}

void cancelCommand() {
	s_inCommand = 0;
	s_uartRcvBufferPos = 0;
}

uint8_t handlePotentialCommand(char c) {
	if(!s_backslashReceived 
		&& !s_inCommand
		&& s_uartRcvBufferPos == 0) {
		//wait for the beginning
		if(c != '\\') {
			return 0;
		}
		s_backslashReceived = 1;
		return 0;
	}
	if(s_backslashReceived) {
		s_backslashReceived = 0;
		if(c != 'c' && c != 'C') {
			return 0;
		}
		s_inCommand = 1;
		return 0;
	}
	if(s_inCommand) {
		if(c == '/') {
			uint8_t numCmds = handleCommands();
			return numCmds;
		}
		s_uartRcvBuffer[s_uartRcvBufferPos] = c;
		s_uartRcvBufferPos++;
		if(s_uartRcvBufferPos >= RECEIVER_BUFF_SIZE) {
			cancelCommand();
		}
	}
	return 0;
}

void handleUart() {
	uint8_t resultErrorCode = 0;
	do {
		cli();
		uint16_t getResult = uart_getc();
		sei();
		uint8_t c = (uint8_t)getResult;
		resultErrorCode = (uint8_t)(getResult >> 8);
		
		if (resultErrorCode == 0) {
			uart_putc(c);
			if(handlePotentialCommand(c)) {
				resetControllerTimeout();
			}
		}
	} while(resultErrorCode == 0);
}

void stopAll() {
	Motor_setSpeedPercent(&s_mainMotor, 0);
	Servo_setPercent(50);
	TimeoutMotor_setDirection(&s_featureMotor1, 1);
	TimeoutMotor_setSpeedPercent(&s_featureMotor1, 0);
	TimeoutMotor_setRemaining(&s_featureMotor1, 0);
	TimeoutMotor_setDirection(&s_featureMotor2, 1);
	TimeoutMotor_setSpeedPercent(&s_featureMotor2, 0);
	TimeoutMotor_setRemaining(&s_featureMotor2, 0);	
}

void handleControllerTimeout() {
	stopAll();
}

int main(void)
{
	char* reason="No known reason\r\n";	
	
	if(MCUCSR & (1<<PORF )) reason = "Power-on reset.\r\n";
	if(MCUCSR & (1<<EXTRF)) reason = "External reset!\r\n";
	if(MCUCSR & (1<<BORF )) reason = "Brownout reset!\r\n";
	if(MCUCSR & (1<<WDRF )) reason = "Watchdog reset!\r\n";
	if(MCUCSR & (1<<JTRF )) reason = "JTAG reset!\r\n";
	
	MCUCSR = 0; //reset power up reason register
	
	uart_init(UART_BAUD_SELECT(UART_BAUDRATE, F_CPU));
	Pin_setMode(&PIN_LED_DEBUG, PinMode_Output);
	Pin_setMode(&PIN_LED_DEBUG2, PinMode_Output);
	Pin_setValue(&PIN_LED_DEBUG2, PinValue_High);
	
	Clock_init(&s_clock, SERVO_TIMER_PERIOD_MS);
	
	Servo_init();
	
	initMotorTimer();
	initMainMotor();
	initFeatureMotor1();
	initFeatureMotor2();
	initStatusLed();
	initLEDs();
	
	RgbLed_setColor(&s_stateLed, 0xFF0000); //Red
	
	TIMSK |= (1<<TOIE0);					// enable timer overflow interrupt 


	stopAll();
	sei();
	
	uart_puts(reason);
	uart_puts("Motor control ready\r\n");
	
	uint16_t delay_ms = 500;
	uint16_t nextMilliseconds = 0;
	uint8_t lastMinute = 0;

	wdt_enable(WDTO_120MS);

	while (42)
	{
		handleUart();
		RgbLed_tick(&s_stateLed);
		
		if(checkControllerTimeoutReached()) {
			handleControllerTimeout();			
		}
		Duration duration = Clock_getDuration(&s_clock);

		uint32_t totalMillisecondsThisMinute = (uint32_t)duration.milliseconds;
		totalMillisecondsThisMinute += (uint32_t)duration.seconds * (uint32_t)1000ul;
		
		if(lastMinute != duration.minutes) {
			lastMinute = duration.minutes;
			nextMilliseconds -= 60ul * 1000ul;
		}
		
		if(totalMillisecondsThisMinute > nextMilliseconds) {
			nextTestStep();
			nextMilliseconds += delay_ms;
		}
		wdt_reset();
	}
	return 0; 								// this line should never be reached
}

ISR(BADISR_vect)
{

    for (;;) uart_puts("!");
}

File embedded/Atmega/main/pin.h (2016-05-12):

#ifndef PIN_H_
#define PIN_H_

#include <stdint.h>

typedef enum {
	PinMode_Output = 1,
	PinMode_Input = 0
} PinMode;

typedef enum {
	PinValue_High = 1,
	PinValue_Low = 0
} PinValue;

typedef struct {
	volatile uint8_t* definitionRegister;
	volatile uint8_t* portRegister;
	uint8_t offset;
} Pin;

typedef struct {
	Pin pin;
	uint8_t counter;
	uint8_t value;
	PinValue lastPinValue;
} SoftPwmPin;

void Pin_init(Pin* pin, volatile uint8_t* definitionRegister, volatile uint8_t* portRegister, uint8_t offset);

void Pin_setMode(Pin* pin, PinMode mode);

void Pin_setValue(Pin* pin, PinValue value);

PinValue Pin_getValue(Pin* pin);

void SoftPwmPin_init(SoftPwmPin* softPwmPin, Pin pin);

void SoftPwmPin_setValue(SoftPwmPin* softPwmPin, uint8_t value);

void SoftPwmPin_tick(SoftPwmPin* softPwmPin);

#endif

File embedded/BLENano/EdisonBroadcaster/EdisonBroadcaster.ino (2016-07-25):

//Board version 1.0.5
#include <BLE_API.h>

BLEDevice ble;

void initBle() {
  //Close peripheral power
  NRF_POWER->DCDCEN = 0x00000001;
  NRF_TIMER1->POWER = 0;
  NRF_TIMER2->POWER = 0;
  NRF_WDT->POWER = 0;
  NRF_TEMP->POWER = 0;
  //NRF_UART0->POWER = 0;

  ble.init();
}

void setup() {
  Serial.begin(115200);
  while(!Serial) {
    delay(10);
  }
  Serial.setTimeout(300);
  initBle();
  Serial.println("EdisonBroadcaster ready!");
}

const static uint8_t EDDYSTONE_FLAGS_DATA[] = { 0x06 };
const static uint8_t EDDYSTONE_HEADER_DATA[] = { 0xAA, 0xFE };
static uint8_t EDDYSTONE_SERVICE_DATA[31];

struct SchemeMapping {
  SchemeMapping(String pScheme, uint8_t pFlag) {
    flag = pFlag;
    scheme = pScheme;
  }
  uint8_t flag;
  String scheme;
};

const static SchemeMapping SCHEME_MAPPINGS[] = {
  //SchemeMapping(String("http://www."), 0x00),
  //SchemeMapping(String("https://www."), 0x01),
  SchemeMapping(String("http://"), 0x02),
  SchemeMapping(String("https://"), 0x03)
};

bool advertiseEddystone(String url) {
  uint8_t urlSchema = 0x02; //http
  for(int i=0; i<sizeof(SCHEME_MAPPINGS); i++) {
    String scheme = SCHEME_MAPPINGS[i].scheme;
    uint8_t flag = SCHEME_MAPPINGS[i].flag;
    if(url.startsWith(scheme)) {
      urlSchema = flag;
      if(scheme.length() == url.length()) {
        url = "";
      } else {
        url = url.substring(scheme.length(), url.length());
      }
      //Serial.println(String("Scheme found: ") + scheme + ", setting flag to: " + String(urlSchema, HEX) + String(", Rest of the URL = ") + url);
      break;
    }
  }

  ble.gap().stopAdvertising();
  ble.gap().clearAdvertisingPayload();
  ble.gap().clearScanResponse();

  //Serial.println("Advertising URL: " + url);

  if(String("").equals(url)) {
    //Serial.println("Detected empty URL!");
    return true;
  }

  uint8_t serviceDataIndex = 0;

  EDDYSTONE_SERVICE_DATA[serviceDataIndex++] = 0xAA; //Eddystone ID 1
  EDDYSTONE_SERVICE_DATA[serviceDataIndex++] = 0xFE; //Eddystone ID 2
  EDDYSTONE_SERVICE_DATA[serviceDataIndex++] = 0x10; //URL
  EDDYSTONE_SERVICE_DATA[serviceDataIndex++] = 0xEB; //power
  EDDYSTONE_SERVICE_DATA[serviceDataIndex++] = urlSchema;

  char urlChars[31];
  url.toCharArray(urlChars, sizeof(urlChars));

  for(int i=0; i<url.length(); i++) {
    if(serviceDataIndex < 30) {
      EDDYSTONE_SERVICE_DATA[serviceDataIndex++] = (uint8_t)urlChars[i];
    }
  }

  uint32_t errorCode = 0;

//  ble.accumulateAdvertisingPayload(GapAdvertisingData::BREDR_NOT_SUPPORTED);
  errorCode = errorCode | ble.gap().accumulateAdvertisingPayload(GapAdvertisingData::FLAGS, EDDYSTONE_FLAGS_DATA /* 0x01 */, sizeof(EDDYSTONE_FLAGS_DATA));
  errorCode = errorCode | ble.gap().accumulateAdvertisingPayload(GapAdvertisingData::COMPLETE_LIST_16BIT_SERVICE_IDS /* 0x03 */, EDDYSTONE_HEADER_DATA, sizeof(EDDYSTONE_HEADER_DATA));
  errorCode = errorCode | ble.gap().accumulateAdvertisingPayload(GapAdvertisingData::SERVICE_DATA /* 0x16 */, EDDYSTONE_SERVICE_DATA, serviceDataIndex);
  
  ble.gap().setAdvertisingType(GapAdvertisingParams::ADV_NON_CONNECTABLE_UNDIRECTED);
  ble.gap().setAdvertisingInterval(100);

  if(errorCode == 0) {
    errorCode = errorCode | ble.gap().startAdvertising();
  }

  return errorCode == 0;
}

const String EDISON_URL_COMMAND = "ec";

bool handleCommand(String command, String param) {
  if(command.equals(EDISON_URL_COMMAND)) {
    if(advertiseEddystone(param)) {
      Serial.println("\\rnc=1/");
    } else {
      Serial.println("\\rnc=0/");
    }
  }
}

void loop() {
  if(Serial.available() > 0) {
     String input = Serial.readStringUntil('\n');
     //echo
     Serial.print(input + "\n");
     input.replace("\r", "");
     if(input.startsWith("\\c")) {
      String commandString = input.substring(2, input.length());
      int equalsIndex = commandString.indexOf("=");
      if(equalsIndex > 0 && equalsIndex < commandString.length()) {
        String command = commandString.substring(0, equalsIndex);
        String param = commandString.substring(equalsIndex + 1, commandString.length() - 1);
        handleCommand(command, param);
      }
     }
  }
}

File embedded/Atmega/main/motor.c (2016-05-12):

#include "motor.h"

void Motor_init(
	Motor* motor,
	Pin pinDirection1,
	Pin pinDirection2,
	uint16_t timerMax,
	volatile uint16_t* timerCounterRegister16,
	volatile uint8_t* timerCounterRegister8,
	uint8_t isInverted,
	MotorMode mode) {
		motor->pinDirection1 = pinDirection1;
		motor->pinDirection2 = pinDirection2;
		motor->timerMax = timerMax;
		motor->timerCounterRegister16 = timerCounterRegister16;
		motor->timerCounterRegister8 = timerCounterRegister8;
		motor->isInverted = isInverted;
		motor->mode = mode;
		
		Pin_setMode(&pinDirection1, 1); //output
		Pin_setValue(&pinDirection1, PinValue_Low);

		Pin_setMode(&pinDirection2, 1); //output
		Pin_setValue(&pinDirection2, PinValue_Low);

		Motor_setDirection(motor, 1);		
		Motor_setSpeedPercent(motor, 0);
} 

void Motor_setDirection(Motor* motor, uint8_t direction) {
	motor->direction = direction;
	Motor_adaptSignal(motor);
}

void Motor_setSpeedPercent(Motor* motor, float percent) {
	if(percent > 100) {
		percent = 100;
	}
	if(percent < 0) {
		percent = 0;
	}
	motor->speedPercent = percent;
	Motor_adaptSignal(motor);
}

void Motor_adaptSignal(Motor* motor) {
	float percent = motor->speedPercent;

	if(motor->mode == MotorMode_DirectPwm) {
		PinValue directionVal = PinValue_Low;
		directionVal = motor->direction == 0 ? PinValue_Low : PinValue_High;

		if(motor->direction == 1) {
			//reverse signal as we are having a 1 as reference
			percent = 100 - percent;
		}
		if(motor->speedPercent == 0) {
			//disable direction pin by setting it to the PWM value
			directionVal = motor->isInverted ? PinValue_High : PinValue_Low;
		}
		Pin_setValue(&motor->pinDirection1, directionVal);		
	} else if(motor->mode == MotorMode_SpeedDirection) {
		PinValue directionVal = PinValue_Low;
		directionVal = motor->direction == 0 ? PinValue_Low : PinValue_High;
		
		if(motor->speedPercent == 0) {
			//disable direction pin by setting it to the PWM value
			directionVal = motor->isInverted ? PinValue_High : PinValue_Low;
		}
		Pin_setValue(&motor->pinDirection1, directionVal);		
	} else if(motor->mode == MotorMode_LeftRightPwm) {
		PinValue directionLeft = PinValue_Low;
		PinValue directionRight = PinValue_Low;
		if(motor->direction == 0) {
			directionLeft = PinValue_High;
		} else {
			directionRight = PinValue_High;
		}
		if(motor->speedPercent == 0) {
			//disable direction pin by setting left and right to 0
			directionLeft = PinValue_Low;
			directionRight = PinValue_Low;
		}
		Pin_setValue(&motor->pinDirection1, directionLeft);
		Pin_setValue(&motor->pinDirection2, directionRight);
	}
	if(motor->isInverted) {
		percent = 100 - percent;
	}
	float value = (motor->timerMax * percent) / 100;
	if(motor->timerCounterRegister16 != 0) {
		*motor->timerCounterRegister16 = (uint8_t)value;
	} else if(motor->timerCounterRegister8 != 0) {
		*motor->timerCounterRegister8 = (uint8_t)value;
	}	
}

void TimeoutMotor_init(
    TimeoutMotor* tMotor, 
    float tickDuration,
    Pin pinDirection1,
	Pin pinDirection2,
	uint16_t timerMax,
	volatile uint16_t* timerCounterRegister16,
	volatile uint8_t* timerCounterRegister8, 
    uint8_t isInverted,
	MotorMode mode) {
    
    Motor_init(&tMotor->motor, pinDirection1, pinDirection2, timerMax, timerCounterRegister16, timerCounterRegister8, isInverted, mode);
    tMotor->tickDuration = tickDuration;
    tMotor->remaining = 0;
    tMotor->speedPercent = 0;
}

void TimeoutMotor_tick(TimeoutMotor* tMotor) {
    if(tMotor->remaining == 0) {
        return;
    }
    tMotor->remaining -= tMotor->tickDuration;
    if(tMotor->remaining <= 0) {
        Motor_setSpeedPercent(&tMotor->motor, 0);
        tMotor->remaining = 0;
    }
}

void TimeoutMotor_setRemaining(TimeoutMotor* tMotor, float remaining) {
    tMotor->remaining = remaining;
    if(tMotor->remaining > 0) {
        Motor_setSpeedPercent(&tMotor->motor, tMotor->speedPercent);
    }
}

void TimeoutMotor_setDirection(TimeoutMotor* tMotor, uint8_t direction) {
    Motor_setDirection(&tMotor->motor, direction);
}

void TimeoutMotor_setSpeedPercent(TimeoutMotor* tMotor, float percent) {
    tMotor->speedPercent = percent;
    if(tMotor->remaining > 0) {
        Motor_setSpeedPercent(&tMotor->motor, percent);
    }
}

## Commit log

2016-02-08 fixed Android Marshmallow "problem" (Bluetooth now needs location permissions) fixed servo angle calculation problem
2016-02-08 added Fritzing diagram for a first wiring schema added one-finger control to the Android app for remote control
    [L298N Circuit.fzz, Wiring.fzz, configure autostart.txt]
2016-02-08 added simple app for Android wear. It is basically a copy of the Android app. A next step would be to a) bundle the wear app to the full app b) extract common components (like the Car handler and the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
    changed the "Ready" state for the Lego car to switch off the lights. This way the lights only get switched on when a central connects
    [Wiring.fzz]
2016-02-08 First implementation of the Raspberry peripherals adapted to the new interface. Modified the Pin configuration to match valid Raspberry pins. Not yet tested.
2016-02-08 added different Bluetooth servie names for Edison and Raspberry. Added logging to the Raspberry PWM implementation. Modified Fritzing diagram to include two new LED-pairs (white) for front and back (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
    [Wiring.fzz]
2016-02-16 added gpio overlay for the raspberry added front fog pin and back drive pin changed GPIO implementations so that they do nothing when they are configured with a value lower than 0
    [Wiring.fzz]
2016-02-22 make the Bluetooth connection survive orientation changes but still kill it when the app is left or when the device list is (re-)entered
2016-02-22 new Fritzing diagram (additional Raspberry Pi variant using a different motor driver)
    [Wiring.fzz]
2016-03-26 first jeep differentiation. Next step: OSAL for Raspberry GPIO and Raspberry WiringPi
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2016-04-21 changed servo logic from software based to hardware based (on timer 0). Timer 1 will controll two additional motors and timer 2 will controll the third motor
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2016-04-24 Added UART lib and added debug output. Fixed clock initialization to use the correct millisecond value (not the tick duration but the period duration) Changed the test logic to not wait 500ms in the 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
    [main.c]
2016-04-26 fixed some bugs added reason of reset/power on output added delay for reading the serial input (stabilizes the system, further investigation needed) added watchdog added support for more commands in 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
    [main.c]
2016-04-28 Added RedBear Duo Arduino project renamed atmega project Fixed ATMega configuration (now it runs stable) Because it is stable now: - removed cycle delay - increased baudrate
    [LegoControl.ino, main.c]
2016-04-29 added Bluetooth service for Speed and Steering. Now the Android control app is able to control the RedBear Duo. => First working version that is able to control the car! Eddystone broadcasting is imp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
    [LegoControl.ino, main.c]
2016-04-30 introduced a ping mechanism so that the AVR notices when the controller isn't sending any more and as a consequence switches everything off
2016-04-30 cleaned up Arduino project by separating the functional modules. Next step: define a BT service structure and make constants for the AVR commands added RGB LED (no PWM for now) for the state
2016-05-02 Beautified Arduino code by using C++ classes for the Bluetooth handling. Used a AVR stl port for Arduino (also included in this commit)
2016-05-05 added commands and functionality for all planned LEDs and both feature motors. Todo: Timeout functionality for the feature motors
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2016-05-06 added millisecond variant of the feature motor timeouts, added rebuild target to the makefile
2016-05-06 added light and feature motor AVR commands to the Duo application. Added Model to the Duo application to handle all the "car business logic" added read option to the Bluetooth service characteristics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
2016-05-06 removed serial debug prints fixed Duo -> Nano communication
    [AVRCommunication.cpp, NANOCommunication.cpp]
2016-05-07 changed the motor control to not use the controllers built in phase and speed mechanism but to directly calculate the pwm and reference signal
2016-05-08 changed prescaler for motors from 1 to 64 (now the driver works a bit better, esp. with the little M motor)
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2016-05-10 added LeftRightPwm mode for motors (not yet tested) added structure diagram with pin definitions to visualize the pin layout of the AVR
2016-05-11 new h bridge for the main motor and the feature motors. Adapted motor mode and pin usage. Reduced motor PWM frequency so that all h bridges are able to handle it. Removed redundant Pin variables
2016-05-12 Code cleanup (using enums for pin values and modes) fixed LeftRightPwm motor control (Left and Right have to go to zero when the speed shall be 0) added Bluetooth characteristics and model logic for 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
    [LegoCarModel.cpp, main.c, motor.c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]
2016-05-13 cleaned up Arduino code (removed some commented out tests) added feature control to the Android app
2016-05-13 revised LED pins (all LEDs that only need one logic are only one pin now). Left two A-Pins open so that they can be used as an ADC input. Added blink pins, logic, commands and Bluetooth characteristic
2016-05-16 Mainboard PCB layout
    [Mainboard.fzz, Mainboard_Elcrow_1.fzz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]
2016-05-16 removed std::string and replaced it by String (from Arduino) fixed BT data read functionality adjusted MovableFrontLight time and speed
    [LegoCarModel.cpp]
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2016-05-17 updated Fritzing diagram and PCB layout.
    [Mainboard.fzz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]
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2016-05-21 updated Mainboard PCB section by adding some more labels
    [Mainboard.fzz]
2016-05-25 added control board layout plan
    [ControlBoard.fzz, Mainboard.fzz]
2016-06-02 BOM, moved Control Board Fritzing file
    [ControlBoard.fzz]
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2016-06-03 Tizen wearable app: implemented steering/speed control and BT connection. Currently the app crashes for whatever reason when the first characteristic writeValue happens.
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2016-06-04 Timen wearable: made app more robust to race conditions. Still the problem of occasionally shrinking ui when switching back from control to list (suspicion: too early bt scan after bt disconnect)
2016-06-12 improved CarModel on RedBear added version of board package and firmware as a comment so the exact environment is reproducible
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2016-07-11 adapted to new Bluetooth API. Only problem: Device disconnect isn't recognized
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2016-07-11 better min, max and offset handling for steering added Racing Truck profile
2016-07-13 added servo offset telegram so that the servo offset gets persisted and used immediately on AVR boot
2016-07-13 added servo offset to the jeep profile added compiler error to force an active profile choose
    [LegoControl.ino]
2016-07-15 updated presentation
    [Mainboard.fzz]
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2016-07-17 added control board variant
    [ControlBoard.fzz]
2016-07-25 RedBear Duo & BLE Nano cleanup + new Profile (Dumper-Michi)
    [ControlBoard.fzz]
2016-07-25 updated PCB layout (labels)
    [Mainboard.fzz]
2016-07-25 fixed min and max angle usage (there wasn't any :) ) adjusted min and max angles for Dumper-Michi profile
    [LegoCarModel.cpp]
2016-07-27 deleted old embedded variant (Raspberry & NodeJS) and renamed new variant (embedded_v2 -> embedded)
    [ControlBoard.fzz, Mainboard.fzz, Mainboard_Elcrow_1.fzz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]
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2016-07-30 removed temporary gerber files
    [Mainboard_Elcrow_1.fzz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]
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2016-07-31 added notes to the control board Fritzing diagram
    [ControlBoard.fzz]
2016-07-31 added notes to the Mainboard (LED channels)
    [Mainboard.fzz]
